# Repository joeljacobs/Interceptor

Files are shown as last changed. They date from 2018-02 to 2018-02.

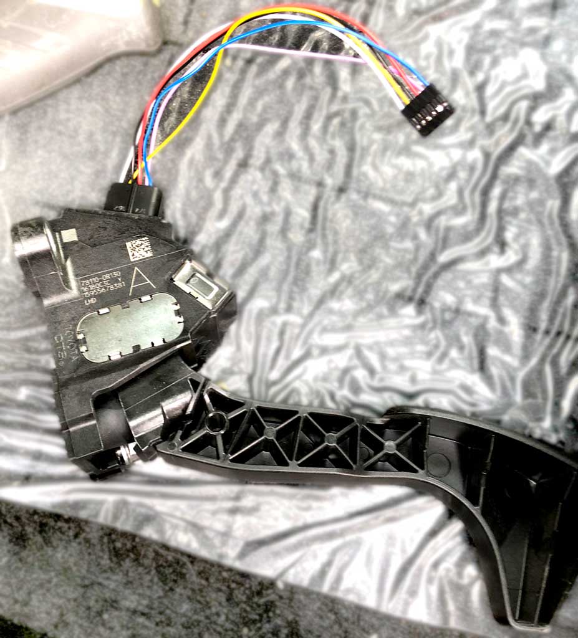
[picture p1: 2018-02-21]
images/GasPedalWhole.jpg

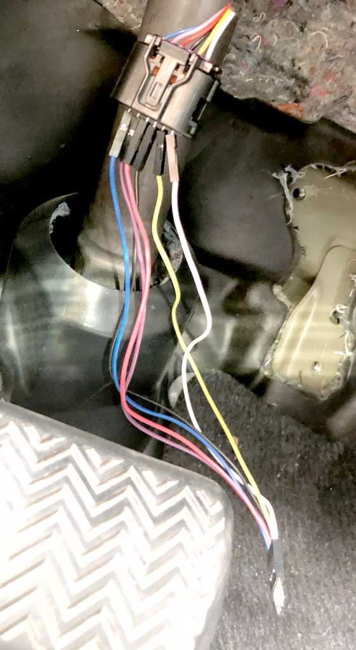
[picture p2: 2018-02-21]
images/GasPedalECUSide.jpg

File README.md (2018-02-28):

# Interceptor
Code and info for a Gas Pedal Interceptor for use with Open Pilot - Now superceded by Comma Pedal! 

### Explanation
The interceptor is used to provide stop-and-go capability on Open Pilot supported cars that don't currently support it. 

A gas pedal interceptor is a device that is placed between an electronic gas pedal and the ECU (Engine Control Unit). It detects the voltage from the gas pedal which represents the pedal's position. It then writes that same voltage back out to the ECU. When Open Pilot takes control, Open Pilot sends the gas position instead.

### History
When Comma originally setup Open Pilot on their Acura, they created their own interceptor to give it stop-and-go capability. However, it was considered a hack, therefore no plans for making interceptors were published.

Comma believes ECU hacks are a more elegant solution to the stop-and-go problem. However skills are required to accomplish such hacks, so it is likely many cars will never get one. This is where the interceptor comes in. When asked about this problem, Comma said their plans for an intercepter weren't ever going to be in any shape to publish, but that if we wanted to build one from scratch, we could create a Slack channel and make it happen. 

Much of the code Comma uses on the Acura still exists in Open Pilot. This means it shouldn't be too difficult to integrate into it. In fact, when asked, George said "It’s probably a 20 line change."

# UDATE: On February 27, 2018 COMMA ANNOUNCED THEIR OWN INTERCEPTOR! THE COMMA PEDAL!
Now that the Pedal exists, this project will flounder. But I'll at least keep the information around. 

### How it works
A prototype is now built using the hardware listed below. It is essentially an Arduino Uno connected to a CAN Bus module and a Digital to Analog Converter. These then connect to the gas pedal, the ECU and the CAN bus.  

The gas pedals for most modern cars output 0 to 5 volts representing pedal position. We feed the 0-5V into the Arduino's analog-to-digital ports. We then send the voltage back out to the ECU using the D-to-A chip. There are actually two redundant 5V analog signals, so we have to capture and send the voltage twice. 

Open Pilot communicates using the CAN bus. So we must send the pedal position to Open Pilot via CAN, and read back OP's gas commands from CAN as well. 

### Status
The prototype is built and installed in a Rav4. It currently handles all gas pedal relaying just fine. It can also read and write on the CAN bus. We're using the CAN id's Comma originally used.

We had to add the ID's to fingerprints.py and the dbc file. 

#### To Do
* Search OP code to find out what it needs from the Interceptor, and excactly what it will send.
* Alter OP code to use the interceptor
* Alter Arduino code.

### Hardware
Included in this repository is a diagram used to make a circuit board to hold the D-to-A and the pins for easy removal.

We used standard breadboarding jumper wires instead of trying to purchase the correct connectors for the gas pedal. That means poking male jumper wires into the female holes of the connector, and sliding female jumper wires into the male pins of the conector. It holds surprisingly well. We then removed the single Dupont ends from the jumper wires and added multi-conductor ends. This isn't a good permanent solution, but it works well for prototyping. 

Finally, the CAN module we used is not ideal. We could have probably done away with the circuit board if we would have instead used the CAN Shield in the list below. We've since purchased one, but not built with it yet. Another down-side to the one we used is that it required a custom Arduino library. The Can Shield probably doesn't. 

#### D-to-A chip: Microchip MCP4822
https://www.digikey.com/product-detail/en/microchip-technology/MCP4822-E-P/MCP4822-E-P-ND/951465

#### CAN Module I used:
https://www.amazon.com/gp/product/B015W4D9WY/ref=oh_aui_detailpage_o01_s01?ie=UTF8&psc=1

#### CAN Arduino Shield that I should have probably used instead:
https://www.amazon.com/gp/product/B06XWQ4WF9/ref=oh_aui_detailpage_o05_s00?ie=UTF8&psc=1

#### OBDII splitter:
https://www.amazon.com/gp/product/B017IBP1MK/ref=oh_aui_detailpage_o01_s00?ie=UTF8&psc=1

#### Altered Arduino library for the Can Module (This library is altered to use the slower clock on the specific module, generic library should be fine for the shield):
https://github.com/Flori1989/MCP2515_lib

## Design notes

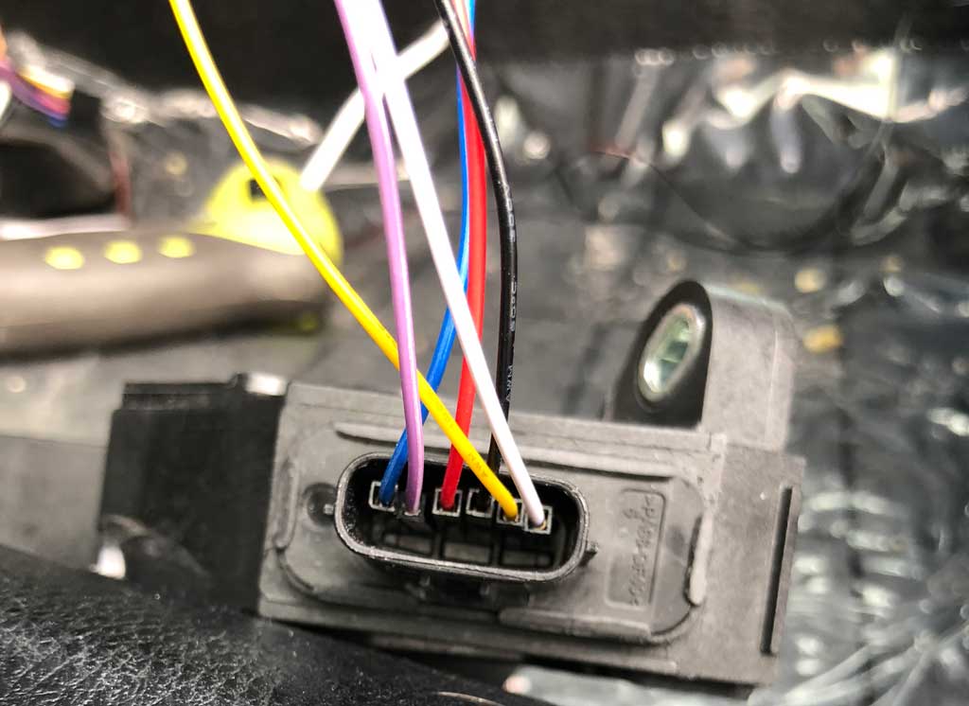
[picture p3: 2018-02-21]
images/GasPedalJumperWiressm.jpg

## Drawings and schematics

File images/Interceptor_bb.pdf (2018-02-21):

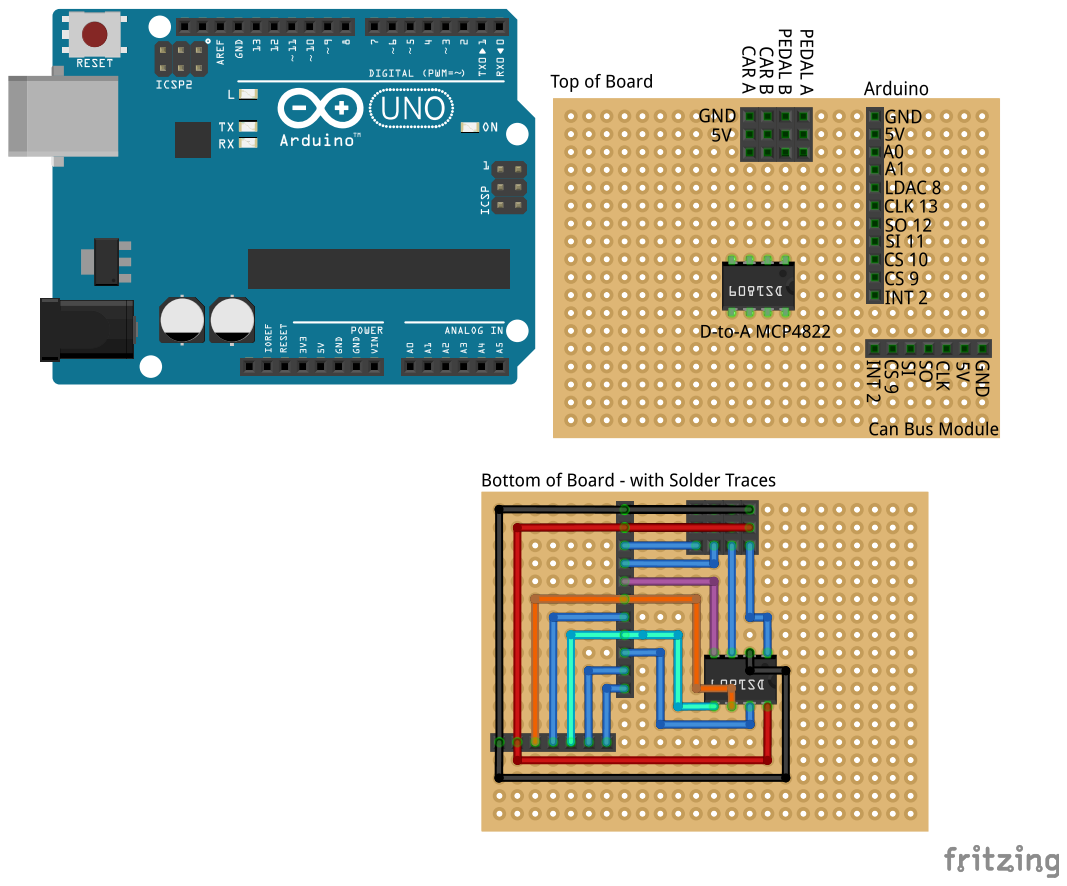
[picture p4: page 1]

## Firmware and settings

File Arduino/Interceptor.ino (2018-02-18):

#include <SPI.h>
//#include <mcp_can.h>
 
//ADA
const int PIN_CS = 10;
const int GAIN_1 = 0x1;
const int GAIN_2 = 0x0;
unsigned int pedal0 = 0;
unsigned int pedal1 = 0;

////CAN
//const int SPI_CS_PIN = 9;
//unsigned char flagRecv = 0;
//unsigned char len = 3;
//unsigned char buf[8];
//unsigned long interval=100; // the time we need to wait
//unsigned long previousMillis=0; // millis() returns an unsigned long.
//unsigned char stmp[5] = {0, 0, 0, 0, 0};
//MCP_CAN CAN(SPI_CS_PIN); 
//
////SERIAL INPUT (UNUSED)
//char receivedChar;
 
void setup()
{
  Serial.begin(115200);
 //SPI (ADA & CAN)
  SPI.begin();  
  SPI.setClockDivider(SPI_CLOCK_DIV2);
  
 //ADA
  pinMode(PIN_CS, OUTPUT);
  pinMode(A0, INPUT);
  pinMode(A1, INPUT);
  PORTB &= 0xfE; //latch LDAC by taking pin 8 low
  
// //CAN
//    while (CAN_OK != CAN.begin(CAN_1000KBPS))              // init can bus : baudrate = 1000                                                                                                                                                                                                                                                                                                                                                                                                                                                                                                                                                                                                                                                                                                                                                                                                                                                                                                                                                                                                                                                                            00k
//    {
//        Serial.println("CAN BUS Shield init fail");
//        Serial.println(" Init CAN BUS Shield again");
//        delay(100);
//    }
//    Serial.println("CAN BUS Shield init ok!");
//
//  attachInterrupt(2, MCP2515_ISR, FALLING); // start interrupt for can
//  CAN.init_Mask(0, 0, 0x3ff);                         // there are 2 mask in mcp2515, you need to set both of them
//  CAN.init_Mask(1, 0, 0x3ff);
//  CAN.init_Filt(0, 0, 0x200); //0x200
}

//ADA Output
void setOutput(byte channel, byte gain, byte shutdown, unsigned int val)
{
  byte lowByte = val & 0xff; //sends lower 8 bits of 12-bit value (& oxff means make everything a 1 except what val has as a zero - to clear?)
  byte highByte = ((val >> 8) & 0xff) | channel << 7 | gain << 5 | shutdown << 4;
   
  PORTB &= 0xfb; //PORTB means bankB on the arduino. this sends a 1 to bankB pin 3, which is pin 10 - joel thinks this is backwards - sends a 0
  SPI.transfer(highByte);
  SPI.transfer(lowByte);
  PORTB |= 0x4; //this sends a 0 to bankB pin3 which is pin 10. - Joel thinks this is backwards - sends a 1
}

////CAN INTERRUPT FUNCTION
//void MCP2515_ISR()
//{
//    flagRecv = 1;
//}
//
////SERIAL INPUT (unused)
//void recvOneChar() {
//    if (Serial.available() > 0) {
//        receivedChar = Serial.read();
//    }
//}

//MAIN LOOP
void loop()
{
  //ADC ---------------------------------------------------------------
  pedal0 = analogRead(A0) * 4 *1.24;
  pedal1 = analogRead(A1) * 4 *1.24;
  
  if (pedal0 > 3199) //3700
  {
    pedal0 = 3199;
  }
  if (pedal1 > 3999) //4500
  {
    pedal1 = 3999;
  }
  setOutput(0, GAIN_2, 1, pedal0);
  setOutput(1, GAIN_2, 1, pedal1);

  //PORTB &= 0xfE; //latch LDAC by taking pin 8 low
  //PORTB |= 0x1; //unlatch LCAC by taking pin 8 high

//  //CAN ----------------------------------------------------------------
//  unsigned long currentMillis = millis(); // grab current time
//  //check if "interval" time has passed (1000 milliseconds)
//  if ((unsigned long)(currentMillis - previousMillis) >= interval) {
//    
//    // send data:  id = 0x10, standrad frame, data len = 8, stmp: data buf
//    stmp[0] = ((pedal0 >> 8) & 0xff);
//    stmp[1] = pedal0 & 0xff;
//    stmp[2] = ((pedal1 >> 8) & 0xff);
//    stmp[3] = pedal1 & 0xff;
//    //stmp[4] = 0b00101001; //counter starts two bits in and is 2 bits, cksum is next 4 bits
//    stmp[4] = 0b01010101;
//    CAN.sendMsgBuf(0x201, 0, 5, stmp);
//    
//    previousMillis = millis();
//  }
//
//  if(flagRecv)                   // check if get data
//      {
//
//        flagRecv = 0;                // clear flag
//        CAN.readMsgBuf(&len, buf);    // read data,  len: data length, buf: data buf
//
//        Serial.println("\r\n------------------------------------------------------------------");
//        Serial.print("Get Data From id: ");
//        Serial.println(CAN.getCanId());
//        for(int i = 0; i<len; i++)    // print the data
//        {
//            Serial.print("0x");
//            Serial.print(buf[i], HEX);
//            Serial.print("\t");
//        }
//        Serial.println();
//
//      }
}

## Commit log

2018-02-09 lowered max voltage for gas
2018-02-10 Added latching of analog out with pin 8
2018-02-10 Dropped max gas output to .5v less than max
2018-02-21 Added images
    [Interceptor.fzz]
